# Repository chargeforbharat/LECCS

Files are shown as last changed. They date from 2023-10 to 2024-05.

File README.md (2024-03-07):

# LECCS repository 

## Introduction
 
'Light Electric Combined Charging System' is an open source charging standard aimed at making interoperability of charging easy and seamless.
LECCS is the charging standard comprising of two parts

1. Connector specification  
    * Specified under IS-17017 : Part2 : Section 7  
2. Communication protocol  
    * Specified under IS17017 : Part 31   

## License and usage
 LECCS repository is the collection of information such as links to connector specification, specification documents (drawings, CAD), related firmware/software SDKs etc, for LECCS.  
 LECCS is one of the standards adopted by the Charge For Bharat consortium.  

 Copyright &copy; 2023 LECCS - Light Electric Combined Charging System

 This repository contains free information: you can redistribute it and/or modify
 it under the terms of the GNU General Public License as published by
 the Free Software Foundation, either version 3 of the License, or
 (at your option) any later version.  
 This repository is distributed in the hope that it will be useful,
 but WITHOUT ANY WARRANTY; without even the implied warranty of
 MERCHANTABILITY or FITNESS FOR A PARTICULAR PURPOSE.  
 See the GNU General Public License for more details.
 You should have received a copy of the GNU General Public License  along with this repository.  If not, see [https://www.gnu.org/licenses/]

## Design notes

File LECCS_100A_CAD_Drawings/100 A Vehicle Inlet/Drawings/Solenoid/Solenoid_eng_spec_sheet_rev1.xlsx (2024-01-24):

 |  | Main Specifications
S# | Specification | Description | Typical / Standard | Min | Max | Units
Functional
1 | Operating Voltage | DC voltage polarity reversed on the same wires for lock and unlock | 12 | 9 | 12.5 | V
2 | Operating Current | Pulse (<300 ms) | - | - | 3 | A
3 | Holding Force/Releasing Force | Solenoid Actuation Force | 10 | 7 | 12 | N
4 | Plunger Displacement |  | 5 |  |  | mm
5 | Plunger Length (unlock) | From the mounting surface | 7.5 | 7.3 | 7.8 | mm
6 | Plunger Length (lock) | From the mounting surface | 12.5 | 12.3 | 12.8 | mm
7 | Plunger diameter |  | 4 |  |  | mm
8 | Failure force | Failure of plunger in case of abuse | 45 |  |  | kg
9 | Feedback Switch | Actuated during ON/OFF for state recognition (lock & unlock) | - | - | - | -
10 | Feedback Switch Operating states | Solenoid in Lock | Contact Closed | - | - | -
11 |  | Solenoid in Unlock | Contact Open | - | - | -
12 | Feedback Switch applied Voltage |  | 3.3 |  |  | V
13 | Feedback Switch applied Current |  | - | 0.5 | 100 | mA
14 | Feedback Switch Resistance | Open State | - | 1 | - | M Ohms
15 |  | Close State | - |  | 0.2 | Ohms
16 | Manual Operation | Manual override | - | - | - | -
17 | Manual Override operating force | Lever pulling force | 10 | 7 | 12 | N
Environmental
1 | Ingress Protection | Part level | IP 54 | - | - | -
3 | Operating Temperature |  | 30 | -20 | 70 | °C
4 | Random Vibration | 10 years of use with no critical failures with on road vibrations. Tested as per Indian city conditions |  |  |  | ATS26
5 | Mechanical Shock | 10 years of use with no critical failures with potholes and curb stones Tested as per Indian city conditions |  |  |  | ATS 11
6 | Corrosion | 5 years of use with no user noticable degradation 10 years of use with no critical failures Tested as per worst Indian coastal city conditions |  |  |  | ATS23
7 | Resistane to vehicle fluids | Protection against Petrol/Diesel, Greases, Vehicle washing chemicals, Transmission fluids, Engine oil etc. | - | - | - | -
8 | Dielectric breakdown Strength (For Switch only) | 100V rms applied for 60 seconds across two terminals | Flash-over shall not occur | - | - | -
9 | Insulation Resistance Test - For Switch (b/w body and terminal) | 500V DC applied for 10 seconds | - | 1 | - | MΩ
Safety
1 | Breakdown voltage (For Switch only) | 100V rms applied for 60 seconds across two terminals | Flash-over shall not occur
2 | Insulation Resistance (For Switch only) | 500V DC applied for 10 seconds wrt Charging pannel |  | 1 |  | MΩ
Operating Modes
1 | Powered | Charging ON | Lock | - | - | -
 |  | Charging OFF | Unlock
2 | Manual | Override manual actuation/Charging OFF | Unlock | - | - | -
Compliance
 | AIS 138 | Vehicle level only
Protections
1 | Freefall damage protection | Freefall damage protection during assembly and handling | - | - | - | Drop from 3 feet height in all six directions
2 | Damage protection | Damage protection during shipping and Storage | - | - | - | Shipping Random vibration test as per ASTM D4728/ISTA 3A and Drop test as per ASTM D4728/ISTA 3A
3 | Fire Protection | Fire resistance materials |  |  |  | Flamability Test UL 94 V-1
Interactions & Communications
 | NA
Realibility
1 | ON OFF Cycles |  |  | 10000 |  | Cycles
2 | Lifetime |  |  | 10 |  | Years
3 | IPHV | Issues per 100 units over lifetime | 1
Serviceability
1 | Service center Replaceable
2 | Field resetable (Manual override)
All others
1 | Wire Pull force | Wire to Casing and Connector | - | 5 | - | Kg
2 | Connector | Besmak 4MW 090 FHCL (BLACK)
3 | Individual Wire Cross Section | FLYR B, PVC, 100deg C | 0.35 |  |  | sqmm
4 | Individual Wire Insultion dia | FLYR B, PVC, 100deg C | 1.3 | 1.2 | 1.4 | mm
5 | Terminal | TT 1378
6 | Connector seal | 281934-4
7 | Wire legth | Wire length (Connector length excluded) | 250 | 240 | 260 | mm
8 | Wire colors | Drawing Attached
9 | Pin Maping | Drawing Attached
10 | Core cable specifications | Diameter | 5 | 4.8 | 5.2 | mm
11 | Reset wire length | Wire Length | 150 | 135 | 165 | mm
12 | Lock/Unlock Sound | TBD
13 | Torque | Screw tightening torque | 0.5 | 0.4 | 0.6 | N-m
14 | Weight | Solenoid assembly weight with Pigtail |  |  | 80 | gm

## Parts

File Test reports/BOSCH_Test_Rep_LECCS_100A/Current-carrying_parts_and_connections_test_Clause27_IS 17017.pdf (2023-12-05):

From | Our reference | Phone | E-Mail
MS/ENB3 | Prijo Ulahannan | +91 80 6783 6100 | Prijo.ulahannan@in.bosch.com | Date: 18-Aug-2022 Report No.: Ather_06_TR
Page 1 of 4 Confidential | Test Report | © BGSW reserves all rights even in the event of industrial property rights.

We reserve all rights of disposal such as copying and passing on to third parties.
Report template V1 (05/25/2022)
Report: | Test report
Title: | Current-carrying parts and connections test
Customer: | Ather India

Document approval

| Name | Signature | Version
Prepared by | Prijo Ulahannan | | 1.0
Reviewed by | Mahantesh Ramannavar

### 1. Issues (situation, motivation and tasks)

The Ather Company has designed and developed a charging connector for electric vehicles, which is patented. Ather has approached Bosch (BGSW) to validate the charging connector between the vehicle and the charging station according to IS 17017 selective tests as prescribed by Ather requirements.

Current-carrying parts, other than terminals (Wire element) were used for test. The task was to check the current-carrying parts, other than terminals which is used and criteria are as per IS 17017 chapter no.27.5 to check the functionality of the samples.

### 2. Results, short version

| | o.k. | not o.k.
2.1 | Material properties of current-carrying parts, other than terminals (Wire) | ☒ | ☐

The overall result of the examined samples is:

☒ Positive
☐ Negative: No further analysis required

Recommendation for further work: NA

MS/ENB3 | Prijo Ulahannan | +91 80 6783 6100 | Prijo.ulahannan@in.bosch.com | Date: 18-Aug-2022 Report No.: Ather_06_TR
Page 2 of 4 Confidential | Test Report | © BGSW reserves all rights even in the event of industrial property rights.

### 3. Conclusions and consequences

All samples have passed the test. All the test parameters are within the specified limit of assessment criteria.

### 4. Results, long version

4.1 Material properties of current-carrying parts, other than terminals – OK (See chapter 5.4 for criteria)

4.1.1 Shall be either of copper.

4.1.2 An alloy containing at least 50 percent copper.

### 5. Details

### 5.1 Part details:

Sl. No. | Description | Part number | Manufacture date / Received date | Remarks
1 | FLRYB 25 Sqmm | ----- | July-2022 | -
2 | FLRYB 0.5 Sqmm | ----- | July-2022 | -

### 5.3 Sample preparation, test setup and test details:

1. Visual inspection of all the samples before test.
2. Visual inspection of samples for the material checks under microscope performed.
3. Data sheet for the wire is checked for material used.
4. Martial composition check has made under X-Ray scope.
5. Same procedure was followed for the all the other samples.
6. See chapter 6 enclosure for more details

### 5.4 Test conditions and assessment criteria:

### 5.4.1 Material properties current-carrying parts, other than terminals

Current-carrying parts, other than terminals, shall be either of,
a) Copper.
b) An alloy containing at least 50 percent copper
c) Other metal no less resistant to corrosion than copper and having mechanical properties no less suitable.

Compliance is checked by inspection if need chemical analysis.

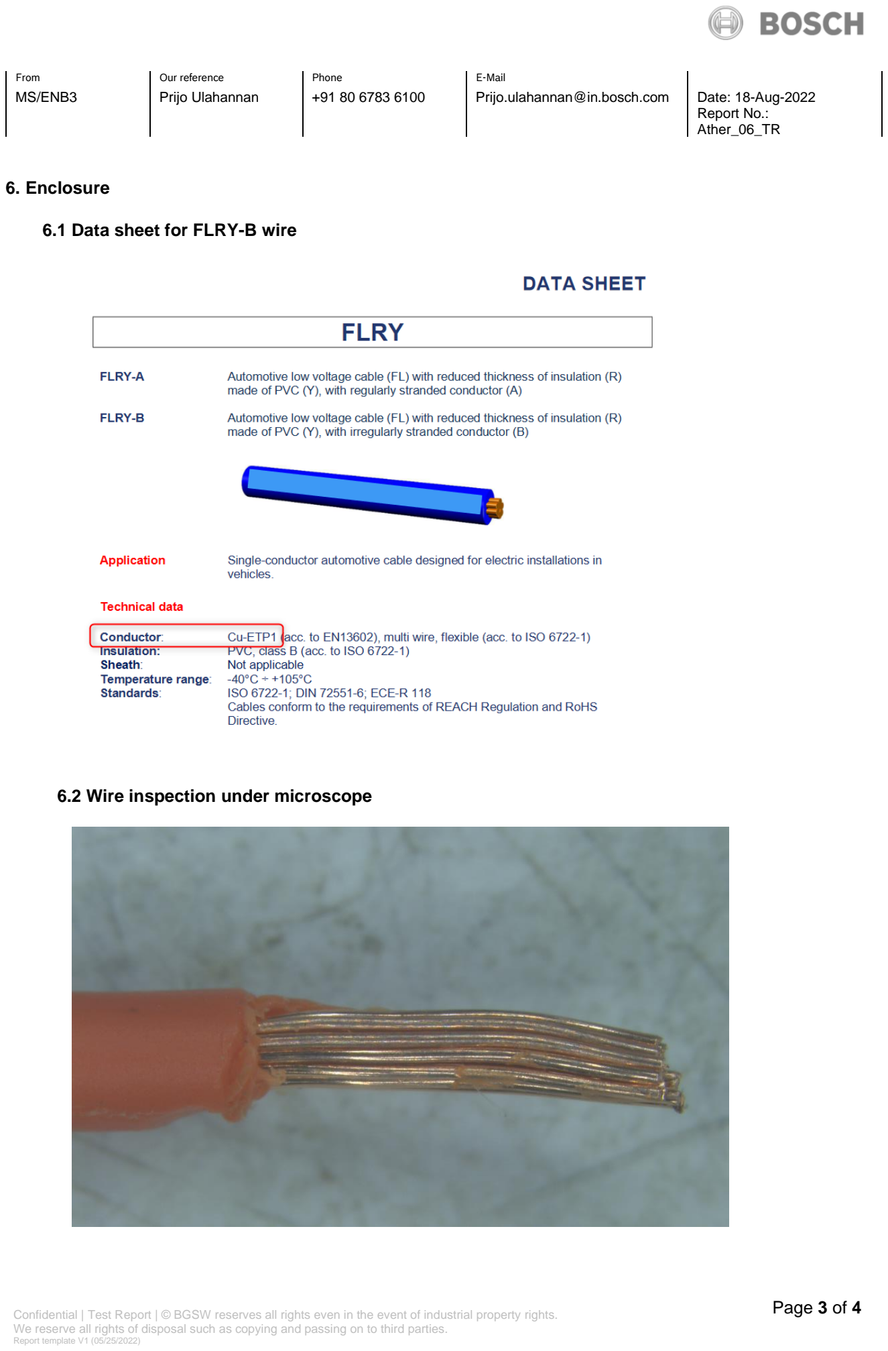
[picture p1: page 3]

MS/ENB3 | Prijo Ulahannan | +91 80 6783 6100 | Prijo.ulahannan@in.bosch.com | Date: 18-Aug-2022 Report No.: Ather_06_TR
Page 3 of 4 Confidential | Test Report | © BGSW reserves all rights even in the event of industrial property rights.

### 6. Enclosure

### 6.1 Data sheet for FLRY-B wire

### 6.2 Wire inspection under microscope

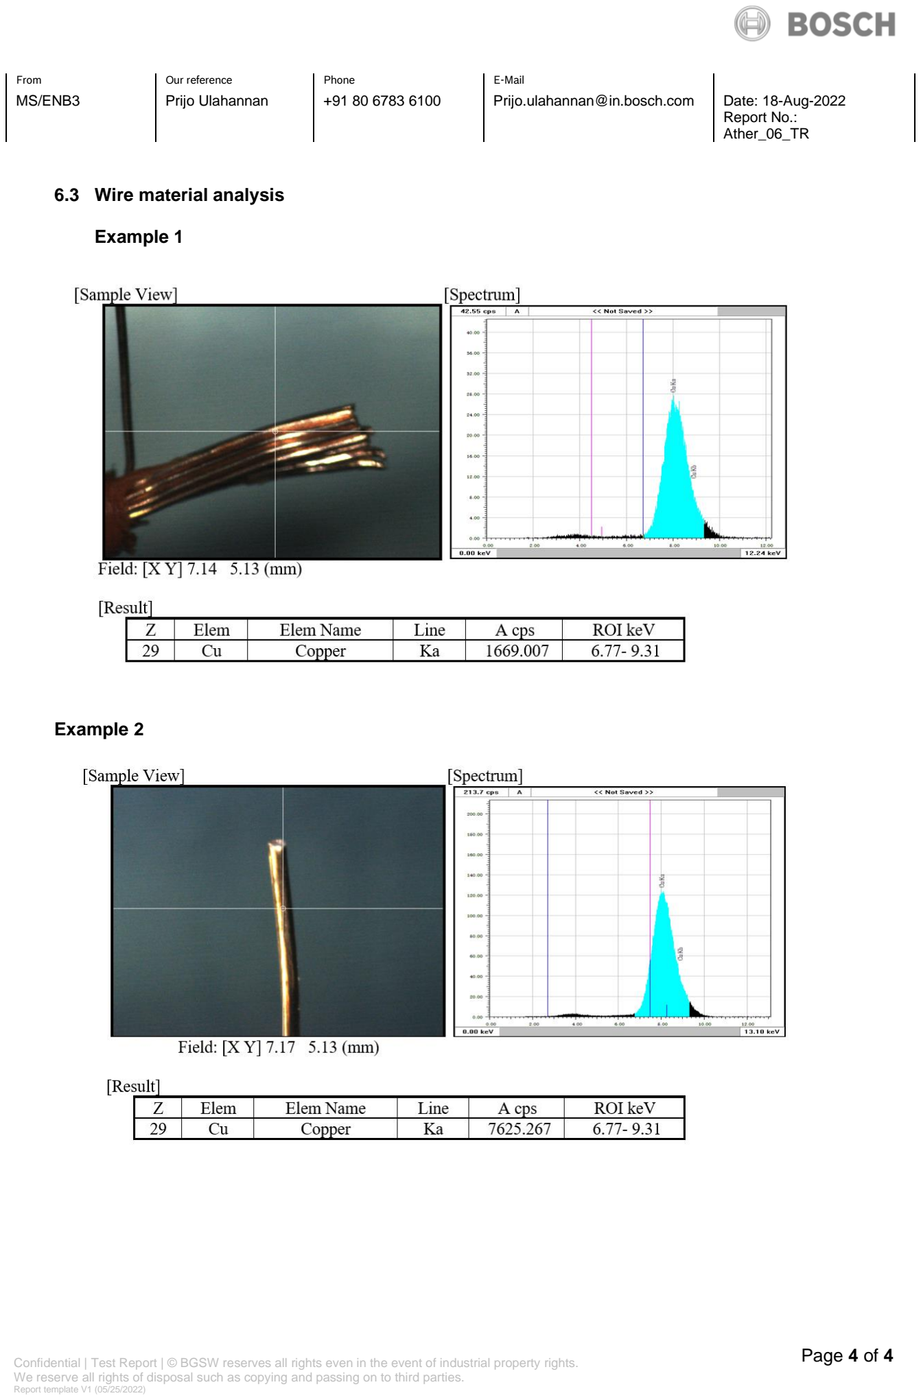
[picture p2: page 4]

MS/ENB3 | Prijo Ulahannan | +91 80 6783 6100 | Prijo.ulahannan@in.bosch.com | Date: 18-Aug-2022 Report No.: Ather_06_TR
Page 4 of 4 Confidential | Test Report | © BGSW reserves all rights even in the event of industrial property rights.

### 6.3 Wire material analysis

Example 1

Example 2

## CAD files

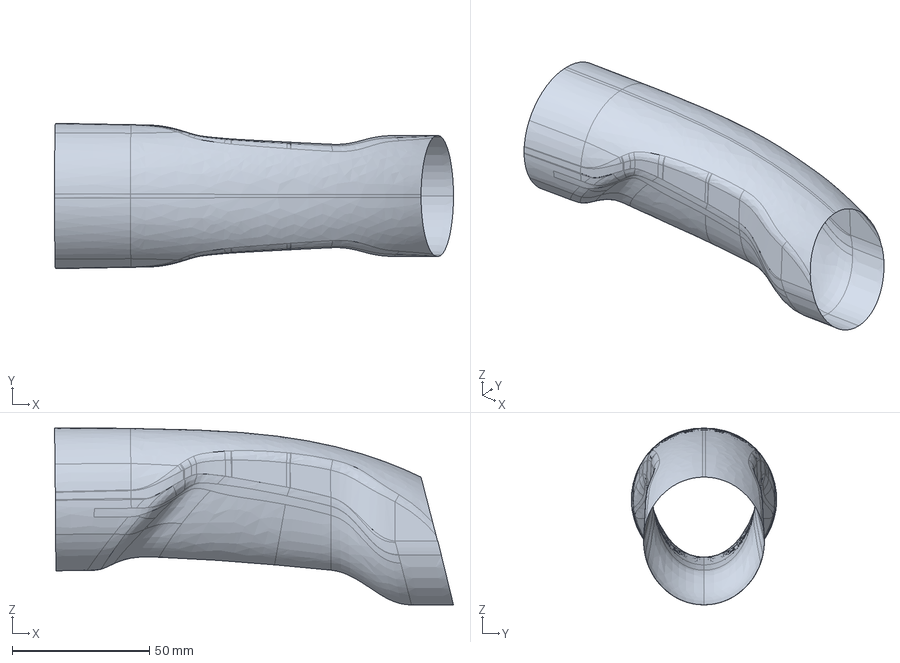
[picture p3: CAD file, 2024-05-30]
LECCS_100A_CAD_Drawings/100 A Charging Handle/Charging Handle/Handle surface.igs
145.5 x 53.0 x 64.5 mm

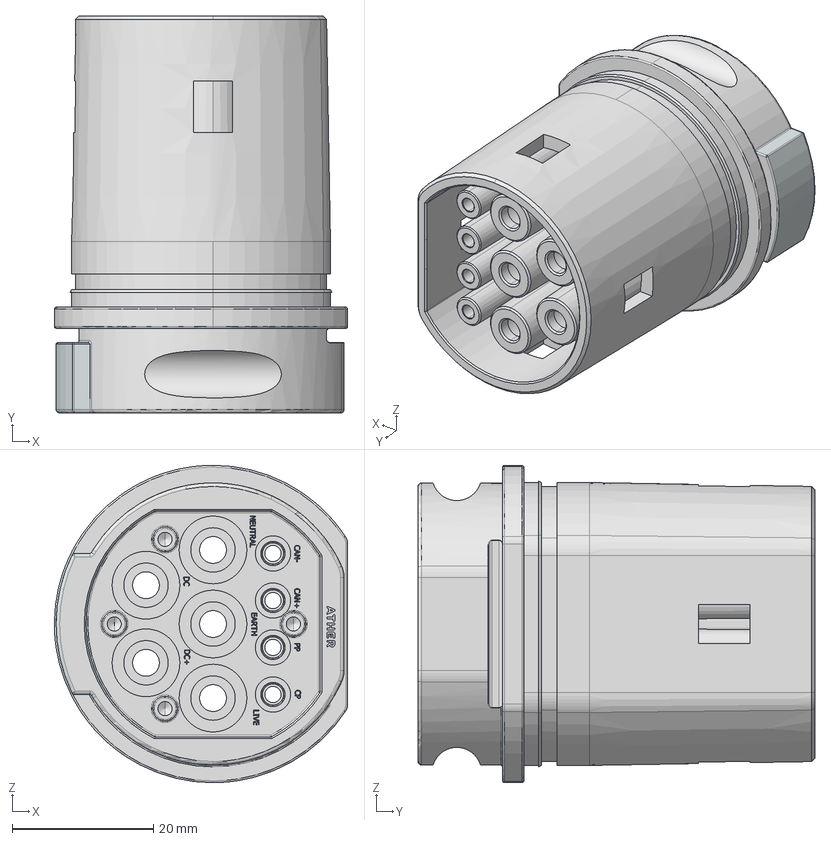
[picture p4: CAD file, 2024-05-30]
LECCS_100A_CAD_Drawings/100 A Charging Handle/Charging Handle/BE5101A004ANN_D_STEP (1).stp
41.6 x 56.3 x 45.0 mm

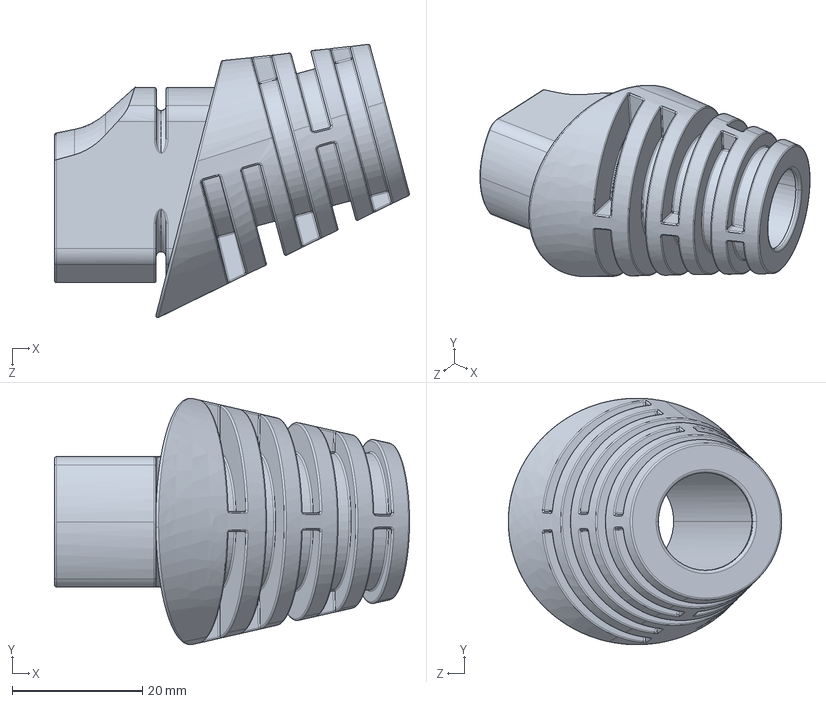
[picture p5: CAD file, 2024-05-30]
LECCS_100A_CAD_Drawings/100 A Charging Handle/Charging Handle/PB00000641-02.STEP
54.5 x 37.8 x 42.0 mm

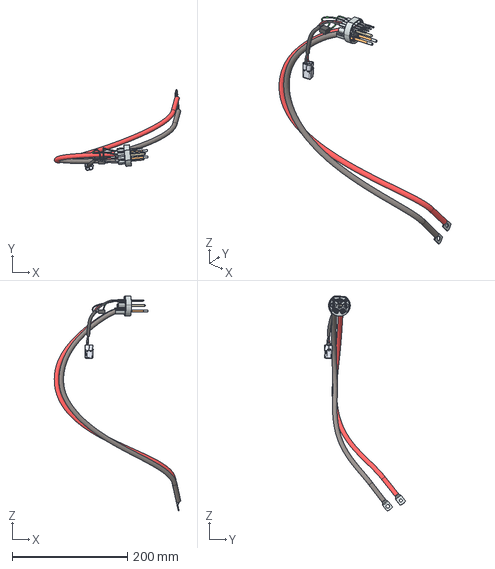
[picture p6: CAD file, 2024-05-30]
LECCS_100A_CAD_Drawings/100 A Vehicle Inlet/CAD/EP00000127_03_STEPSelected_Objs.stp
219.9 x 141.0 x 373.7 mm

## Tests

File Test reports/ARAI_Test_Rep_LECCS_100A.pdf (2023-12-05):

DEVELOPMENT TEST REPORT | CONFIDENTIAL

Report No. ARAI/AED/20222023/3100013430/DT/5075
Dated: 27-JUN-2022
1.0 Name and Address of the | Customer | M/s. ATHER ENERGY PRIVATE LIMITED 3RD FLOOR TOWER D, IBC KNOWLEDGE PARK, BANNERGHATTA MAIN ROAD, BANGALORE-560029, KARNATAKA, INDIA
2.0 | Customer Letter Reference | Email dated: 21-MAR-2022
3.0 | Test Objective | Testing of DC EV vehicle connector (charging gun) and vehicle inlet (for light electric vehicles) according to IS 17017-2-1.
4.0 Condition of the Test | Component | The test components were received in good condition.
5.0 Description of the Device Under | Test (DUT) | DC EV Charging gun and Vehicle inlet
5.1 | Make | Ather Energy Private Limited
| Part numbers | 340A0021532, 340A0021531
DUT Photos

6.0

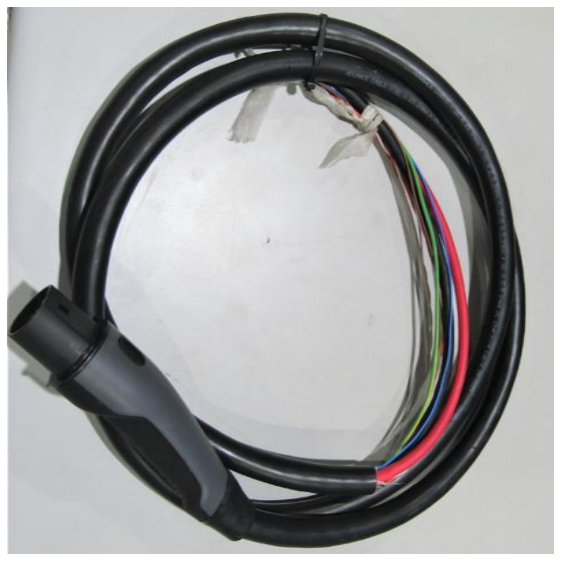
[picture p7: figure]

Result:

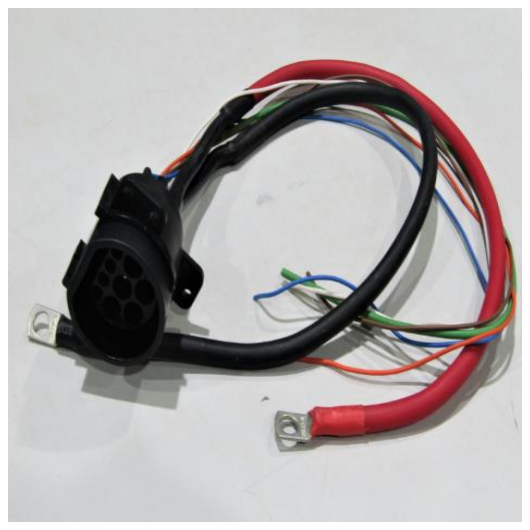
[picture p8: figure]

The DC EV Charging gun and vehicle inlet (for light electric vehicles) serial numbers: “340A0021532, 340A0021531” meets the requirements as per clause 8.0(Test results) of this report

A A MURUMKAR
ENGINEER

A B MULAY
GENERAL MANAGER

A A DESHPANDE
Sr. Dy. DIRECTOR & HoD

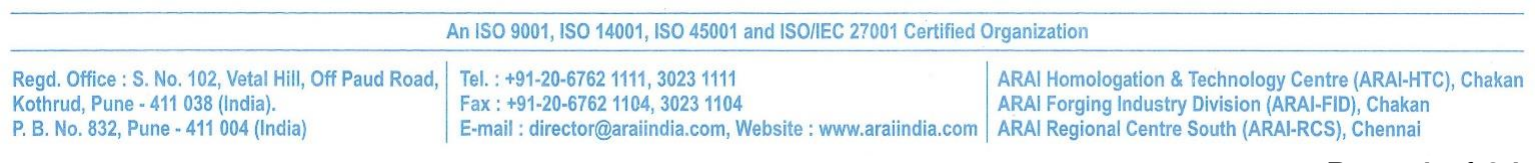
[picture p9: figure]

Report No. ARAI/AED/20222023/3100013430/DT/5075 | CONFIDENTIAL
Dated: 27-JUN-2022

### 7.0 DUT Details:

General product information:
The DUT submitted for the test is a DC EV charging gun and vehicle inlet for Light electric vehicles, Ratings:120V DC Max, 100Amp DC Max current
Number of poles: 9 poles (CP, PP, CAN HIGH, CAN LOW, DC+, DC-, PE) + 2 dummy poles

### 8.0 Test Results:

Sr. No | Test Title | Annex No. | Complies (Yes/No/ N/A)
1.0 Tests and verifications as per IS17017-2-1 | Clause no 10 of this report. | -- | Yes
2.0 | Electrical tests as per IS17017-2-1. | 01 | Yes
3.0 | Environmental/ Climatic tests as per IS17017-2-1. | 02 | Yes
4.0 | Mechanical tests | 03 | Yes

A A MURUMKAR
ENGINEER

A B MULAY
GENERAL MANAGER

_______________________________________________________________________________

This test report pertains only to the components / parts / assemblies / vehicles etc., actually tested at ARAI in the presented condition based on the documents / information produced / submitted by the customer. The issuance of this test report alone does not indicate any measure of approval, certification, supervision, control of quality surveillance by ARAI of the product. No extract, abridgement or abstraction from this test report shall be published or used to advertise the product without the written consent of the Director, ARAI, who reserves the absolute right to agree or reject all or any of the details of any items of publicity for which consent may be sought. ARAI is in no way responsible for any misuse of copying of any design / type / system in connection with entire vehicle/components/parts and assemblies. Breach of any statutory provision of Indian laws or laws of other countries, will be the sole responsibility of the customer and ARAI shall not be liable for any claims or damages, made by the party, whatsoever. The customer shall alone be liable for the same and undertakes to indemnify ARAI in this regard. Further, the ARAI has the right to initiate cancellation / withdrawal of the certificate / report issued, in case of any fraud, misrepresentation, when it surfaces and comes in the knowledge of ARAI. The appropriate local courts at Pune shall have the jurisdiction in respect of any dispute, claim or liability arising out of this report.
Place of Issue: ARAI-HTC, Pune

### 9.0 Connector Photos:

Charging gun Part no: 340A0021532 | Vehicle Inlet Part no: 340A0021531

Markings:

A A MURUMKAR
ENGINEER

A B MULAY

GENERAL MANAGER

### 10.0 Requirements as per IS17017-2-1

Sr. no | Test requirement/specifications | Observation/Remark
1 | Ratings
1.1 | Preferred rated operating voltage ranges: | 120VDC Max
1.2 | Preferred Rated Currents | 100A DC Max
1.3 | Rated Current for Signal or Control Purposes | Rated current for signal or control purposes is 2 A.
1.4 | Accessories suitable or not Suitable for Making and Breaking an Electrical Circuit Under Load | Not suitable for making and breaking an electrical circuit under load
1.5 | Accessories Suitable for, or not Suitable for, Making and Breaking an Electrical Circuit Under Load | Complies
1.6 | Connection between the power supply and the electric vehicle:
2 | General
2.1 | Types of Vehicle Connectors | DC EV Charging gun and vehicle inlet, as declared by customer
2.2 | Basic Interface | DC interface as declared by customer

A A MURUMKAR
ENGINEER

A B MULAY
GENERAL MANAGER

Sr. no | Test requirement/specifications | Observation/Remark
3 | Classification of Accessories
3.1 | According to the Method of Connecting the Conductors | Non-rewireable
3.2 | According to Serviceability | Non-serviceable accessories
3.3 | According to Electrical Operation | Accessories not suitable for making and breaking an electrical circuit under load
3.4 | According to Interface | DC interface, as declared by customer
3.5 | According to the Locking and Interlock Functions
3.6 | According to Locking Facilities | Lockable means provided.
3.7 | According to Interlock Facilities | Means of latching provided, Interlock on vehicle side
3.8 | According to the Presence of Shutter(s) | Without shutters
4 | Marking
4.1 | Accessories shall be marked with: a) Rated current(s) in amperes for power, b) Rated maximum operating voltage(s) in volts, c) The relevant symbol for degree of protection, d) Either the name or trade mark of the manufacturer | Markings provided

A A MURUMKAR
ENGINEER

A B MULAY
GENERAL MANAGER

Sr. no | Test requirement/specifications | Observation/Remark
4.2 | For vehicle connectors, the marking for either the name or trade mark of the manufacturer or the responsible vendor and the type reference, catalogue number or designation shall also be on the outside of the accessory, visible to the user. | Markings provided
4.3 | For all accessories, the marking for the maximum rated operating voltage range and rated current shall be in a place which is visible before installation of the accessory. | Markings provided
4.4 | Markings shall be indelible and easily legible. | Compiles
5 | Dimensions
5.1 | Accessories shall comply with the appropriate standard sheets | Customer specific design for light electric vehicles DC charging. Drawings sheet provided by the customer
5.2 | It shall not be possible to engage vehicle connectors with vehicle inlets having different ratings, or having different contact combinations unless safe operation is ensured or other means are provided to ensure safe operation. | Complies

A A MURUMKAR
ENGINEER

A B MULAY
GENERAL MANAGER

Sr. no | Test requirement/specifications | Observation/Remark
6 | Protection against electric shock
6.1 | Accessories shall be so designed that live parts of vehicle connectors, when they are wired as in normal use, and live parts of plugs and vehicle inlets, when they are in partial or complete engagement with the complementary accessories, are not accessible. | Complies Live parts not accessible.
6.2 | Accessories shall be so designed that, it should follow contact sequencing for connection and disconnection of vehicle connector | Complies
6.3 | It shall not be possible to inadvertently assemble either the part carrying plug or inlet contacts into the enclosure of a socket-outlet or vehicle connector or the part carrying the vehicle connector contacts into the enclosure of a plug or inlet. | Assemblies are Non-rewireable
7 | Size and colour of protective earthing conductors
7.1 | The conductor connected to the protective earthing terminal shall be identified by the colour combination green-and-yellow. | 2.5 sqmm protective conductor provided.
7.2 | The nominal cross-sectional area of the protective earthing conductor and of the neutral conductor,

A A MURUMKAR
ENGINEER

A B MULAY
GENERAL MANAGER

Sr. no | Test requirement/specifications | Observation/Remark
8 | Provision for Earthing
8.1 | Accessories are provided with a protective earthing contact and a protective earthing terminal. | Provided
8.2 | Protective earthing contacts are directly and reliably connected to the protective earthing terminals. | Complies
8.3 | Earthing contacts are shrouded or guarded against mechanical damage | Complies
9 | Accessories with interlock
9.1 | Accessories classified in “not suitable for making and breaking an electrical circuit under load” shall be provided with an interlock. | Interlock provided
9.2 | Vehicle couplers with interlocks shall be so constructed that:
9.2.1 | a vehicle connector cannot be completely withdrawn from the vehicle inlet while the contacts of that vehicle connector are live | Complies
9.2.2 | the contacts of the vehicle connector cannot be made live until the vehicle connector is in proper engagement
9.2.3 | The power contacts shall not make or break under load

A A MURUMKAR
ENGINEER

A B MULAY
GENERAL MANAGER

Sr. no | Test requirement/specifications | Observation/Remark
9.3 | Pilot Contacts and Auxiliary Circuits
9.3.1 | Pilot contacts and auxiliary circuits used for interlocks shall make after the neutral and phase(s) are made. | Complies
9.3.2 | Pilot contacts and auxiliary circuits used for interlock shall break before the phase(s) and neutral are broken. | Complies
10 | General Construction
10.1 | Accessible surfaces of accessories shall be free from burrs, flashes and similar sharp edges. | No sharp edges, burrs
10.2 | Vehicle connectors when mounted as in normal use and without a plug and vehicle inlet respectively in position shall ensure the degree of protection specified on its marking. | Complies
10.3 | Contacts shall be so designed as to ensure adequate contact pressure when completely engaged with the corresponding accessory | Complies
10.4 | Enclosures and parts of accessories providing protection against electric shock shall have adequate mechanical strength | Complies
10.5 | It shall not be possible to remove these parts without the aid of a tool. | Complies
10.6 | Cable entries shall allow the introduction of the conduit or the protective covering of the cable to afford complete mechanical protection. | Complies

A A MURUMKAR
ENGINEER

A B MULAY
GENERAL MANAGER

Sr. no | Test requirement/specifications | Observation/Remark
10.7 | Insulating linings, barriers and the like shall have adequate mechanical strength. | Complies
10.8 | A gripping surface shall be provided | Provided
11 | Construction of Vehicle connectors
11.1 | The enclosure of vehicle connectors shall completely enclose the terminals and the ends of the flexible cable. | Complies
11.2 | Parts of a connector do not work loose during normal use | No loosening observed
11.3 | Connectors cannot be dismantled without a tool | Complies
11.4 | Vehicle connectors incorporate means to meet the marked degree of protection when engaged with the vehicle inlet | Complies
11.5 | Means provided to meet the marked degree of protection are securely fixed to the connector | Complies
12 | Degree of Protection
12.1 | IP rating marked on device | IP44
12.2 | All accessories shall be proof against humid conditions which may occur in normal use. | Complies
13 | Insulation resistance and dielectric strength
13.1 | Insulation resistance | Resistance observed R>5MΩ
13.2 | Dielectric Strength test | Test performed at 2kV, No break down or flashover observed

A A MURUMKAR
ENGINEER

A B MULAY
GENERAL MANAGER

Sr. no | Test requirement/specifications | Observation/Remark
13.3 | Normal Operation
13.3.1 | Normal operation cycles in no load 10,000 cycles | After test observation: 1. No detached part 2. No deterioration of enclosures or barriers; 3. No damage to the entry holes for the plug contacts that might impair proper working 4. No loosening of electrical or mechanical connections 5. No seepage of sealing compound 6. The continuity between mating signal and pilot contacts are maintained.
14 | Flexible cable and their connection
14.1 | Vehicle connectors shall be so designed that the conductors are relieved from strain, including twisting, where they are connected to the terminals or terminations, and that their covering is protected from abrasion. | Flexible cables provided
14.2 | The construction shall ensure that the cable cannot touch accessible metal parts or internal metal parts | Complies
15 | Requirements for vehicle connectors
15.1 | Non-rewireable vehicle connectors
15.1.1 | Non-rewireable vehicle connectors shall be provided with a suitable flexible cable | Provided

A A MURUMKAR
ENGINEER

A B MULAY
GENERAL MANAGER

Sr. no | Test requirement/specifications | Observation/Remark
16 | Mechanical strength
16.1 | Accessories shall have adequate mechanical strength so as to withstand the stresses imposed during installation and use. | Complies
17 | Change of temperature test
17.1 | Temperature test of IEC 60068-2-14, test procedure Nb | See Annexure no: 02 No deformation observed
18 | Resistance to heat
18.1 | Accessories are resistant to heat | See Annexure no: 02 No impairing was observed. Markings still visible after the test
18.2 | Devices are heated in cabinet for 1 hour at a temperature of 110 + 5°C and comply with all criteria at the end of the exposure
19 | Vehicle drive over
19.1 | A plug or vehicle connector shall have adequate resistance to damage from being driven over by a vehicle | See Annexure no: 03. No severe cracking, breaking or deformation observed
19.2 | Accessories wired with the min. size cable of a type recommended by the manufacturer shall be placed on a concrete floor in any normal position of rest
20 | Ratings
20.1 | A component shall be used in accordance with its rating established for the intended conditions of use | Complies
20.2 | Mechanical Assembly
20.2.1 | Loosening of parts in an accessory as a result of vibration due to storage, handling and operation shall not result in a risk of fire, electric shock, injury to persons | Complies

A A MURUMKAR
ENGINEER

A B MULAY
GENERAL MANAGER

ANNEXURE 01

### 1.1 TEST SPECIFICATIONS

TEST DETAILS | ELECTRICAL TESTS AS PER IS 17017-2-1
TEST LOCATION | AED, ARAI-HTC

### 1.2 LABORATORY ENVIRONMENT TEST CONDITIONS

Ambient
temperature | + 25.5°C. | ---- | Relative humidity | 48.5%RH. | ----

### 1.3 INSULATION RESISTANCE AND DIELECTRIC WITHSTAND TEST

Test date: 25-MAR-2022
Test Requirement:
The insulation resistance shall be not less than 5 MΩ.
Dielectric withstand test at 2000V, No flashover or breakdown shall occur during the test. Insulation resistance (IR) test results/observation:
Test parameters | Test voltage applied | Observation
Between all poles connected together and the body | 500 | IR ≥ 5 MΩ
Between each pole in turn and all others, these being connected to the body | 500 | IR ≥ 5 MΩ

Dielectric withstand test results/observation:

Test parameters | Test voltage applied | Observation
Between all poles connected together and the body | 2000 | No flashover or breakdown observed during the test.
Between each pole in turn and all others, these being connected to the body | 2000 | No flashover or breakdown observed during the test.

A A MURUMKAR
TEST ENGINEER

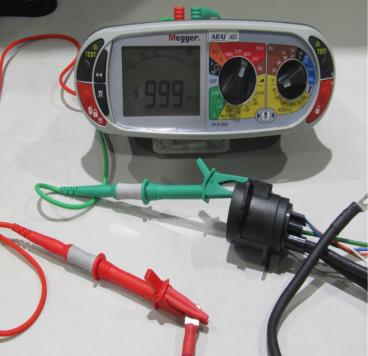
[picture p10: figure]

### 1.4 Temperature Rise test as per IS17017-2-1

Test Date: 25-MAR-2022

### 1.4.1 Test Requirements/Parameters:

1. Test performed at rated 100VDC, 100Amp current for 1 hour as declared by the manufacturer, to measure the temperature rise.
2. Test setup was done as per the normal use case of the vehicle inlet and the charging gun.
3. The maximum permissible temperature of those parts of the plug and the vehicle connector that can be grasped during normal operation, when tested with the accessory carrying the maximum rated current, shall not exceed
- 50 °C for metal parts,
- 60 °C for non-metal parts.
4. For parts which may be touched but not grasped the permissible temperature are
- 60 °C for metal parts,
- 85 °C for non-metal parts.

### 1.4.2 Test setup:

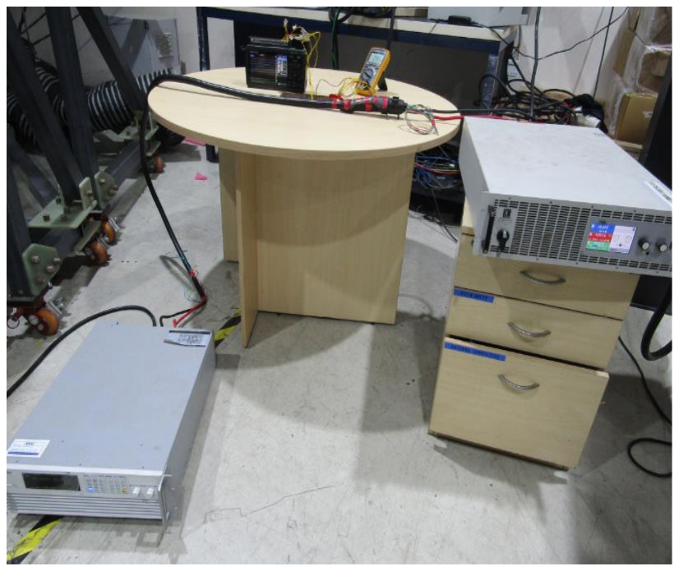
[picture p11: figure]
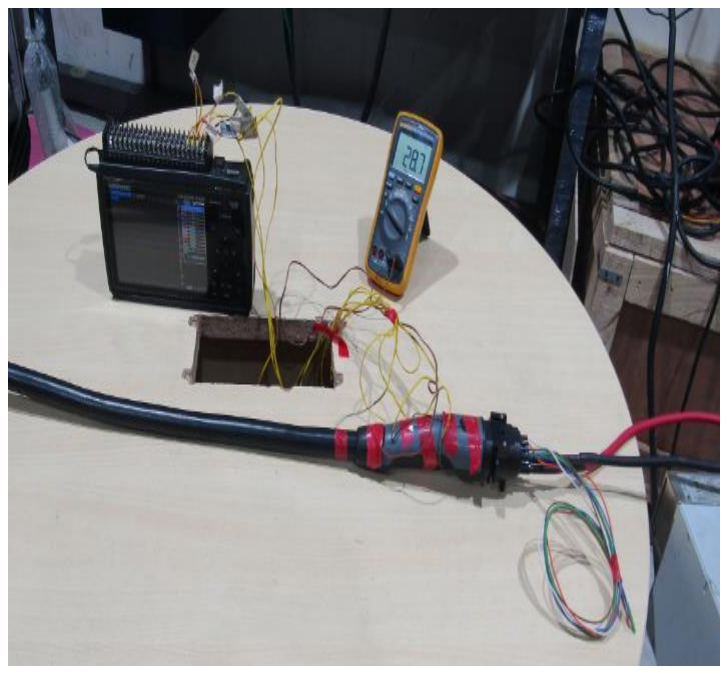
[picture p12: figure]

A A MURUMKAR
TEST ENGINEER

### 1.4.3 Test Result:

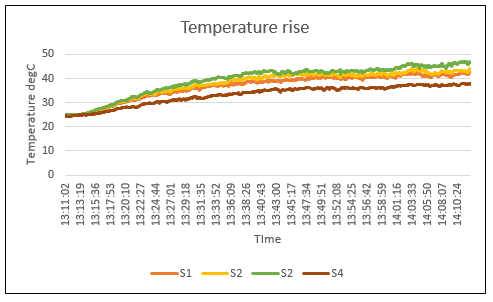
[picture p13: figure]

1.4.4Test observation:

1. The temperature rise of terminals did not exceed 50 degC
2. Surface temperature in normal use meets the requirements as per clause 1.4.1

A A MURUMKAR
TEST ENGINEER

### 1.5 CONTACT SEQUENCE TEST

Test date: 25-MAR-22
Test Requirement:
To check contact sequence of the control and power pins
Test Result/Observation:
The contact sequence observed while inserting the vehicle connector is: First contact: Protective earthing (PE)
Second contact: DC Power contacts (DC+ and DC-)
Third contact: Proximity detection (PP)
Fourth contact: Control pilot (CP) and CAN pins (CAN HIGH, CAN LOW)

While withdrawing the vehicle connector:
First release: Control pilot (CP) and CAN pins (CAN HIGH, CAN LOW) Second release: Proximity detection (PP)
Third release: DC Power contacts (DC+ and DC-)
Fourth release: Protective earthing (PE)

Contact sequencing achieved with different terminal lengths in-order to meet the requirements as

per standard.
Contact terminals photos:
Charging gun terminals: | Vehicle inlet terminals:

A A MURUMKAR
ENGINEER

A B MULAY
GENERAL MANAGER
End of Annexure 01

ANNEXURE 02

### 2.1 TEST SPECIFICATIONS

TEST DETAILS | ENVIRONMENTAL/CLIMATIC TESTS AS PER IS 17017-2-1
TEST LOCATION | AED, ARAI-HTC

### 2.2 LABORATORY ENVIRONMENT TEST CONDITIONS

Ambient
temperature | + 25.5°C. | ---- | Relative humidity | 48.5%RH. | ----

### 2.3 CHANGE OF TEMPERATURE TEST

Test date: 24-MAR-2022

Test Requirement:
Accessories with insulated end cap on the contacts shall not be adversely affected by the temperature stress conditions which may occur in normal use.

Test parameters:
Temperature test of IS 9000 (Part 14/Sec 2) with following parameters:
a) Test procedure: Nb;
b) Lower temperature (TA): -30°C;
c) Higher temperature (TB): 100°C;
d) Slew rate: 3 K/min;
e) Exposure time (t1): 1 h; and
f) Number of cycles: 5.

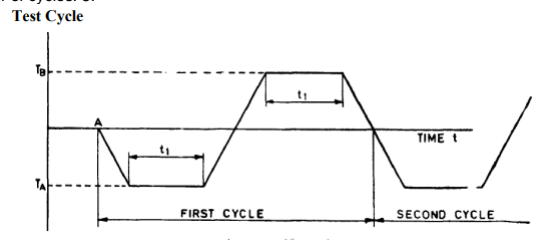
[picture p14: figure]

Test Result/Observation:
No deformation observed after the end of test

A A MURUMKAR
TEST ENGINEER

### 2.4 RESISTANCE TO HEAT TEST

Test date: 24-MAR-2022

Test Requirement:
Accessories shall be sufficiently resistant to heat.

Test parameters:
The samples are kept for 1 hour in a heating cabinet at a temperature of 110°C ± 5 K.

Test Result/Observation:
No impairing observed.
No sealing flow observed.
Markings are legible
Test Setup:

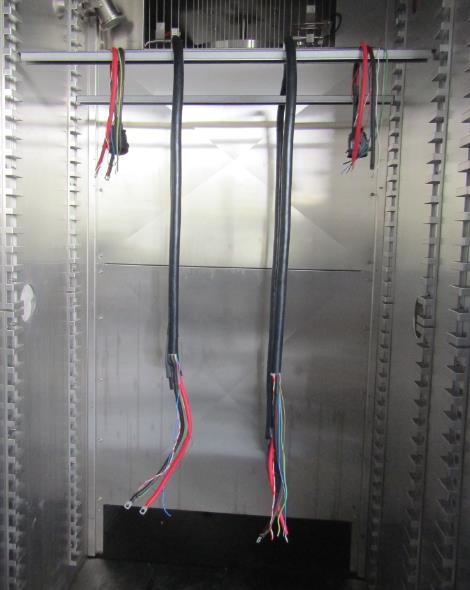
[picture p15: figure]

A A MURUMKAR
TEST ENGINEER

### 2.5 HUMIDITY STORAGE TEST

Test date: 05-APR-2022

Test Requirement:
All accessories shall be proof against humid conditions which may occur in normal use.

Test parameters:
The humidity treatment is carried out in a humidity cabinet containing air with a relative humidity maintained between 91 percent and 95 percent. The temperature of the air, at all places where samples can be located, is maintained within 1°C of any convenient value T between 20°C and 30°C for 168 hrs
After test:
Markings should be legible
Required IR ≥5MΩ
Test Setup:

Test result:

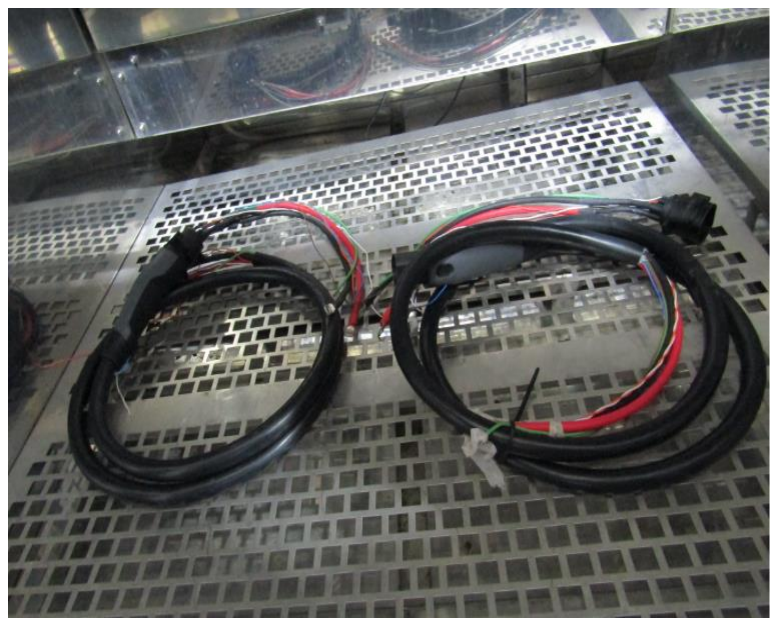
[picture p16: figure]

Measured IR was found to be ≥5MΩ
Markings are legible, and no impairing or sealant flow observed

A A MURUMKAR
TEST ENGINEER

A B MULAY
GENERAL MANAGER
End of Annexure 02

ANNEXURE 03

### 3.1 TEST SPECIFICATIONS

TEST DETAILS | MECHANICAL TESTS
TEST LOCATION | AED, ARAI-HTC

### 3.2 LABORATORY ENVIRONMENT TEST CONDITIONS

Ambient
temperature | + 25.5°C. | ---- | Relative humidity | 48.5%RH. | ----

### 3.3 VEHICLE DRIVE OVER TEST

Test date: 18-APR-2022
Test Requirement:
1. A plug or vehicle connector shall have adequate resistance to damage from being driven over by a vehicle, unless it is provided with a cable management system which prevents the accessory from being left on the ground.
2. The wheel is to be rolled over the vehicle connector or plug at a speed of 8 ± 2 km/h. The accessory is to be oriented in a natural resting position before applying the force in a different direction for each sample.
3. There shall be no severe cracking, breakage, or deformation.
Test photo:


A A MURUMKAR
TEST ENGINEER

Test Result/Observation:


1. No severe cracking, breakage, or deformation observed.
2. Measured IR after test was found to be ≥5MΩ.

### 3.4 DROP TEST

Test date: 25-MAR-2022
Test Requirement:
1. Drop test to be performed from a height of 1m on concrete surface, in all directions
2. There shall be no severe cracking, breakage, or deformation.
3. Test performed as per customer requirements
Test photo:


A A MURUMKAR
TEST ENGINEER

Test Result/Observation:


1. No severe cracking, breakage, or deformation observed.
2. Measured IR after test was found to be ≥5MΩ.

### 3.5 CONNECTOR RESISTANCE TO DRAG

Test date: 19-APR-2022
Test Requirement:
1. Drag of charging cable for 1km, to check the insulation and mechanical strength
2. There shall be no severe cracking, breakage, or deformation.
3. Test performed as per customer requirements
Test photo:


A A MURUMKAR
TEST ENGINEER


Test Result/Observation:


1. No severe cracking, breakage, or deformation observed.
2. Measured IR after test was found to be ≥5MΩ.

A A MURUMKAR
TEST ENGINEER

### 3.6 MARKINGS

Test date: 25-MAR-2022
Test Requirement:
1. Markings shall be indelible and easily legible
2. After the humidity treatment, the marking is rubbed vigorously by hand for 15 seconds with a piece of cloth soaked in water and again for 15 seconds with a piece of cloth soaked with petroleum spirit.
Test photo:


Test Result:


After test Markings are indelible and easily legible. Laser printed markings as declared by manufacturer

A A MURUMKAR
TEST ENGINEER


A B MULAY
GENERAL MANAGER
End of Annexure 03
--- END OF TEST REPORT---

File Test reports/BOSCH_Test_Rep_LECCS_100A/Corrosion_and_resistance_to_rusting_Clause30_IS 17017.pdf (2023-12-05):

From | Our reference | Phone | E-Mail
MS/ENB3 | Prijo Ulahannan | +91 80 6783 6100 | Prijo.ulahannan@in.bosch.com | Date: 18-Aug-2022 Report No.: Ather_01_TR
Page 1 of 4 Confidential | Test Report | © BGSW reserves all rights even in the event of industrial property rights.

We reserve all rights of disposal such as copying and passing on to third parties.
Report template V1 (05/25/2022)
Report: | Test report
Title: | Corrosion and resistance to rusting
Customer: | Ather India

Document approval

| Name | Signature
Prepared by | Prijo Ulahannan
Reviewed by | Mahantesh Ramannavar

### 1. Issues (situation, motivation and tasks)

The Ather Company has designed and developed a charging connector for electric vehicles, which is patented. Ather has approached Bosch (BGSW) to validate the charging connector between the vehicle and the charging station according to IS 17017 selective tests as prescribed by Ather requirements.

3 samples of vehicle connector and Vehicle inlet were used for test. The task was to expose the samples to a some of the solutions as specified in standard for a specified duration to check the behavior of connector in corrosive environment. Test and acceptance criteria are as per IS 17017 chapter no. 30 o check the functionality of the samples.

### 2. Results, short version

| | o.k. | not o.k.
2.1 | Visual inspection of plastic parts for cracks and breakage (New condition) | ☒ | ☐
2.2 | Visual inspection of samples for rust after test | ☒ | ☐

The overall result of the examined samples is:

☒ Positive
☐ Negative: No further analysis required

Recommendation for further work: NA

MS/ENB3 | Prijo Ulahannan | +91 80 6783 6100 | Prijo.ulahannan@in.bosch.com | Date: 18-Aug-2022 Report No.: Ather_01_TR
Page 2 of 4 Confidential | Test Report | © BGSW reserves all rights even in the event of industrial property rights.

### 3. Conclusions and consequences

All 3 connector samples have passed the test. All the test parameters are within the specified limit of assessment criteria.

### 4. Results, long version

- Plastic parts and terminals inspected before test for abnormalities like cracks, burrs, rust and breakage. All the samples subjected to test were in good/acceptable condition → OK

After the test Surfaces has no signs of rust – OK (See chapter 5.4 for Criteria)

### 5. Details

### 5.1 Part details:

Sl. No. | Description | Part number | Manufacture date / Received date | Remarks
1 | Vehicle Inlet | 340A0013634 | July-2022 | -
2 | Vehicle connector | 340A0021042 | July-2022 | -

### 5.2 Equipment details:

Sl. No. | Test equipment | Equipment no. | Remarks
1 | Saltwater setup | ATS-032 | Location: External lab (NABL - TC-7419)

### 5.3 Sample preparation, test setup and test details:

1. Visual inspection of plastic parts conducted on all the samples before test.
2. 3 samples of vehicle connector and vehicle inlet equipped with terminals are used for test.
3. All grease is removed from the parts to be tested, by immersion in ethyl acetone, acetone, methylethyl

ketone or an equivalent degreasing agent for 10 min.

4. Then the parts are then immersed for 10 min in a 10 percent solution of ammonium chloride in water at a

temperature of 20°C ± 5 K.

5. After that without drying, but after shaking off any drops, the parts are placed for 10 min in a box containing

air saturated with moisture at a temperature of 20°C ± 5 K.

6. After the parts have been dried for 10 min in a heating cabinet at a temperature of 100°C ± 5 K,
7. Same procedure was followed for all the other samples.
8. See pictures in chapter 6 Enclosure.

MS/ENB3 | Prijo Ulahannan | +91 80 6783 6100 | Prijo.ulahannan@in.bosch.com | Date: 18-Aug-2022 Report No.: Ather_01_TR


Page 3 of 4 Confidential | Test Report | © BGSW reserves all rights even in the event of industrial property rights.

### 5.4 Test conditions and assessment criteria:

Asessemnt Criteria:

After the test Surfaces has no signs of rust

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


Page 4 of 4 Confidential | Test Report | © BGSW reserves all rights even in the event of industrial property rights.

### 6. Enclosure

### 6.1 CORROSION AND RESISTANCE TO RUSTING

Pic 1: Test set up | Pic 2: Test set up

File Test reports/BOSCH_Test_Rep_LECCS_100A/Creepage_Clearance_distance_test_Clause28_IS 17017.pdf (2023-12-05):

From | Our reference | Phone | E-Mail
MS/ENB | Prijo Ulahannan | +91 80 6783 6100 | Prijo.ulahannan@in.bosch.com | Date: 22-Aug-2022 Report No.: Ather_07_TR
Page 1 of 6 Confidential | Test Report | © BGSW reserves all rights even in the event of industrial property rights.

We reserve all rights of disposal such as copying and passing on to third parties.
Report template V1 (05/25/2022)
R&D-Report: | Test report
Title: | Creepage and Clearance Distance Evaluation
Customer: | Ather India

Document approval

| Name | Signature
Prepared by | Prijo Ulahannan
Reviewed by | Mahantesh Ramannavar

### 1. Issues (situation, motivation and tasks)

The Ather Company has designed and developed a charging connector for electric vehicles, which is patented. Ather has approached Bosch (BGSW) to validate the charging connector between the vehicle and the charging station according to IS 17017 selective tests as prescribed by Ather requirements.

Creepage and Clearance Distances are required for the protection against the operating voltages to protect the equipment or user, moreover in case of malfunction of equipment. The criteria are as per IS 17017 chapter no.28.1, 28.3 & 28.4 to check the correct creep and clearance of the samples.

### 2. Results, short version

| | o.k. | not o.k.
2.1 | Evaluation of Creepage and Clearance Distance | ☒ | ☐

The overall result of the examined samples is:

☒ Positive
☐ Negative: No further analysis required

Recommendation for further work: NA

MS/ENB | Prijo Ulahannan | +91 80 6783 6100 | Prijo.ulahannan@in.bosch.com | Date: 22-Aug-2022 Report No.: Ather_07_TR
Page 2 of 6 Confidential | Test Report | © BGSW reserves all rights even in the event of industrial property rights.

### 3. Conclusions and consequences

All samples have passed the test. All the test parameters are within the specified limit of assessment criteria. From the sample cross section it is determined that the minimum clearance provided for the conducting or live parts are more than that of the required creepage and clearance as specified in the specifications. No electric breakdown and No damage on housings or terminals by deformations or melting observed after and withstand voltage test

### 4. Results, long version

4.1 Evaluation of creepage and clearance distances between live parts, with live parts with different polarity and other metallic accessories. → OK (See chapter 5.4 for criteria)

4.1.1 Creepage Distances and clearances in accordance to 28.1 | → OK
4.1.2 Conducting Evaluation is in accordance with IS 15382 part 1 | → OK

4.1.3 No burnt plastic parts were observed after and withstand voltage test (2000V and 50 Hz) → OK

### 5. Details

### 5.1 Part details:

Sl. No. | Description | Part number | Manufacture date / Received date | Remarks
1 | Vehicle Inlet Male and Female Connectors | ----- | August-2022 | -

### 5.2 Sample preparation, test setup and test details:

1. Accessories are designed as per pollution degree 3 according to IS 15382(Part 1).
2. Evaluation of creepage and clearance distance in accordance with IS 15382(Part 1).
3. Visually inspect and measure the shortest distance between live parts, with live parts of opposite polarity and other metal accessories in proximity if any.
4. From the sample cross section it is determined that the minimum clearance provided for the conducting or live parts are more than that of the required creepage and clearance as specified in the specifications

### 5.3 Test conditions and assessment criteria:

1. RMS Voltage Input: 100V.
2. Creepage distance to avoid tracking failure: 1.8 mm.
3. Clearance distance needed: 0.8 mm.
4. Accessories are under the Overvoltage category II.

MS/ENB | Prijo Ulahannan | +91 80 6783 6100 | Prijo.ulahannan@in.bosch.com | Date: 22-Aug-2022 Report No.: Ather_07_TR


Page 3 of 6 Confidential | Test Report | © BGSW reserves all rights even in the event of industrial property rights.

5.3.1 Data table for creepage distances to avoid tracking failure (IS 15382 (Part 1) :2003)

Note: The data marked in red box are of concern for determining the minimum expected Creepage and clearance distance.

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


Page 4 of 6 Confidential | Test Report | © BGSW reserves all rights even in the event of industrial property rights.

### 5.3.2 Data Table for Clearance Distances. (IS 15382 (Part 1) :2003)

Note: The data marked in red box are of concern for determining the minimum expected Creepage and clearance distance.

### 5.3.3 Material properties

1. Material Used: PA66 (DOMAMID FR66)
2. CTI Value of the Material being used: 600.
3. Material Group: I (According to the CTI value).

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


Page 5 of 6 Confidential | Test Report | © BGSW reserves all rights even in the event of industrial property rights.

### 6 Test Images

Inspection of sample connector terminal after test

Connector male part | Connector female part

Inspection of sample connector terminal after test

Connector male part | Connector female part

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

Reference Drawing; Clearance distances of terminals of; housing.; Clearances of the female plug end cross

Page 6 of 6 Confidential | Test Report | © BGSW reserves all rights even in the event of industrial property rights.

connector in proximity after mating with the section to be inserted to male live parts.

Withstand Voltage test set up

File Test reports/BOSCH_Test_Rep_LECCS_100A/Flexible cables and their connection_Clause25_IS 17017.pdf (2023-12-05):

From | Our reference | Phone | E-Mail
MS/ENB3 | Prijo Ulahannan | +91 80 6783 6100 | Prijo.ulahannan@in.bosch.com | Date: 18-Aug-2022 Report No.: Ather_02_TR
Page 1 of 4 Confidential | Test Report | © BGSW reserves all rights even in the event of industrial property rights.

We reserve all rights of disposal such as copying and passing on to third parties.
Report template V1 (05/25/2022)
Report: | Test report
Title: | Flexible cables and their connection
Customer: | Ather India

Document approval

| Name | Signature
Prepared by | Prijo Ulahannan
Reviewed by | Mahantesh Ramannavar

### 1. Issues (situation, motivation and tasks)

The Ather Company has designed and developed a charging connector for electric vehicles, which is patented. Ather has approached Bosch (BGSW) to validate the charging connector between the vehicle and the charging station according to IS 17017 selective tests as prescribed by Ather requirements.

Samples of vehicle connector used for test. The task was to perform pull test on samples, followed by a torque test to evalauate tensile strength of the cable with assembly. Test and acceptance criteria are as per IS 17017 chapter no. 25.3 to check the functionality of the samples.

### 2. Results, short version

| | o.k. | not o.k.
2.1 | Visual inspection of plastic parts for cracks and breakage (New condition) | ☒ | ☐
2.2 | Cable elongation/anchorage after the test | ☒ | ☐
2.3 | No break in electrical connection (Continuity check) after test | ☒ | ☐

The overall result of the examined samples is:

☒ Positive
☐ Negative: No further analysis required

Recommendation for further work: NA

MS/ENB3 | Prijo Ulahannan | +91 80 6783 6100 | Prijo.ulahannan@in.bosch.com | Date: 18-Aug-2022 Report No.: Ather_02_TR
Page 2 of 4 Confidential | Test Report | © BGSW reserves all rights even in the event of industrial property rights.

### 3. Conclusions and consequences

All connector samples have passed the test. All the test parameters are within the specified limit of assessment criteria.

### 4. Results, long version

- Plastic parts and terminals inspected before test for abnormalities like cracks, burrs, rust and breakage. All the samples subjected to test were in good/acceptable condition → OK

Cable elongation/anchorage after the test – OK (See chapter 5.4 for criteria)

Sl No. | Displacement
Sample - 1 | OK
Sample - 2 | OK
Sample - 3 | OK

No break in electrical connection (Continuity check) after test – OK (See chapter 5.4 for criteria)

Sl No. | Continuity Check
Sample - 1 | OK
Sample - 2 | OK
Sample - 3 | OK

### 5. Details

### 5.1 Part details:

Sl. No. | Description | Part number | Manufacture date / Received date | Remarks
1 | Vehicle connector | 340A0021042 | July-2022 | -

### 5.2 Equipment details:

Sl. No. | Test equipment | Equipment no. | Remarks
1 | UTM Machine | ATS-021 | Location: External lab (NABL - TC-7419)

MS/ENB3 | Prijo Ulahannan | +91 80 6783 6100 | Prijo.ulahannan@in.bosch.com | Date: 18-Aug-2022 Report No.: Ather_02_TR


Page 3 of 4 Confidential | Test Report | © BGSW reserves all rights even in the event of industrial property rights.

### 5.3 Sample preparation, test setup and test details:

1. Visual inspection of plastic parts conducted on all the samples before test.
2. 3 samples of vehicle connector assembly are used for the test.
3. The sample is fixed in the test apparatus so that the axis of the cable is vertical where it enters the sample
4. The cable is then subjected 100 times to a pull of the value shown in Table 18. Each pull is applied without

jerks and has a duration of 1s.

5. Immediately afterwards, the cable is subjected to a torque, of the value specified in Table 18.
6. The displacement of the mark on the cable in relation to the the cable anchorage is measured.
7. Continuity check is performed after the test.
8. Same procedure was followed for the all the other samples.
9. See pictures in chapter 6 Enclosure.

### 5.4 Test conditions and assessment criteria:

Asessemnt Criteria:

- During the tests, the cable shall not be damaged.
- After the tests, the cable shall not have been displaced by more than the values indicated in Table 18. (The displacement of the mark on the cable in relation to the the cable anchorage is measured)
- For non-rewirable accessories, there shall be no break in the electrical connections.


MS/ENB3 | Prijo Ulahannan | +91 80 6783 6100 | Prijo.ulahannan@in.bosch.com | Date: 18-Aug-2022 Report No.: Ather_02_TR
Page 4 of 4 Confidential | Test Report | © BGSW reserves all rights even in the event of industrial property rights.

### 6. Enclosure

### 6.1 Pictures

Pic 1: Test set up | Pic 2: Test set up

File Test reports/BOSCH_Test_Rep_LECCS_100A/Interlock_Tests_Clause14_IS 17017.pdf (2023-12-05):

From | Our reference | Phone | E-Mail
MS/ENB3 | Prijo Ulahannan | +91 80 6783 6100 | Prijo.ulahannan@in.bosch.com | Date: 18-Aug-2022 Report No.: Ather_05_TR
Page 1 of 7 Confidential | Test Report | © BGSW reserves all rights even in the event of industrial property rights.

We reserve all rights of disposal such as copying and passing on to third parties.
Report template V1 (05/25/2022)
Report: | Test report
Title: | Interlock withdrawal force test
Customer: | Ather India

Document approval

| Name | Signature
Prepared by | Prijo Ulahannan
Reviewed by | Mahantesh Ramannavar

### 1. Issues (situation, motivation and tasks)

The Ather Company has designed and developed a charging connector for electric vehicles, which is patented. Ather has approached Bosch (BGSW) to validate the charging connector between the vehicle and the charging station according to IS 17017 selective tests as prescribed by Ather requirements.

Samples of vehicle connector and vehicle inlet (With mechanical interlock) used for test were used for test. The task was to check the withdrawal force of the interlock with with specified force values. Test and acceptance criteria are as per IS 17017 chapter no.14.1.5 and 14.1.6 to check the functionality of the samples.

### 2. Results, short version

| | o.k. | not o.k.
2.1 | Visual inspection of plastic parts for cracks and breakage (New condition) | ☒ | ☐
2.2 | Test to check withdrawal force (Only plastic parts with interlock on vehicle inlet) | ☒ | ☐
2.3 | Withdrawal test with 90-degree rotation (Vehicle connector and inlet assembly) | ☒ | ☐

The overall result of the examined samples is:

☒ Positive
☐ Negative: No further analysis required

Recommendation for further work: NA

MS/ENB3 | Prijo Ulahannan | +91 80 6783 6100 | Prijo.ulahannan@in.bosch.com | Date: 18-Aug-2022 Report No.: Ather_05_TR
Page 2 of 7 Confidential | Test Report | © BGSW reserves all rights even in the event of industrial property rights.

### 3. Conclusions and consequences

All connector samples have passed the test. All the test parameters are within the specified limit of assessment criteria.

### 4. Results, long version

- Plastic parts and terminals inspected before test for abnormalities like cracks, burrs, rust and breakage. All the samples subjected to test were in good/acceptable condition → OK

4.1 Test to check withdrawal force (Only plastic parts with mechanical interlock on vehicle inlet) - OK

(See chapter 5.4 for criteria)

Sample - 1 | OK
Sample - 2 | OK
Sample - 3 | OK

### 4.2 Withdrawal test with 90-degree rotation (Vehicle connector and inlet assembly) – OK

(See chapter 5.4 for criteria)

Sample - 1 | OK
Sample - 2 | OK
Sample - 3 | OK

### 5. Details

### 5.1 Part details:

Sl. No. | Description | Part number | Manufacture date / Received date | Remarks
1 | Vehicle Inlet (With locking) | 340A0013634 | July-2022 | -
2 | Vehicle connector | 340A0021042 | July-2022 | -
3 | Vehicle connector (Only plastic) | 340A0003338 | July-2022 | -

### 5.2 Equipment details:

Sl. No. | Test equipment | Equipment no. | Remarks
1 | UTM | ENB/CL/002-1027832 | Location: BGSW

MS/ENB3 | Prijo Ulahannan | +91 80 6783 6100 | Prijo.ulahannan@in.bosch.com | Date: 18-Aug-2022 Report No.: Ather_05_TR


Page 3 of 7 Confidential | Test Report | © BGSW reserves all rights even in the event of industrial property rights.

### 5.3 Sample preparation, test setup and test details:

5.3.1 Test to check withdrawal force (Only plastic parts with mechanical interlock on vehicle inlet)

1. Visual inspection of plastic parts conducted on all the samples before test.
2. 3 samples of vehicle inlets and vehicle connectors are used for test.
3. The connector is inserted into and withdrawn ten times.
4. The connector with interlock is fixed to the support of an apparatus so that the axis of separation is

vertical and the movement is downwards (See chapter 6 for pictures)

5. A force equal to one-tenth of the withdrawal force as per table 9 (See chapter 5.4) is apllied and

maintained for 60s.

6. Same procedure was followed for the all the other samples.

### 5.3.2 Withdrawal test with 90-degree rotation (Vehicle connector and inlet assembly)

1. Visual inspection of plastic parts conducted on all the samples before test.
2. 3 samples of vehicle inlets and vehicle connectors are used for test.
3. The connector is inserted into and withdrawn ten times.
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

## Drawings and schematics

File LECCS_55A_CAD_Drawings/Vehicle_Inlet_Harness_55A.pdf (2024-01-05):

### CONNECTOR DETAILS: 4 PIN-FEMALE

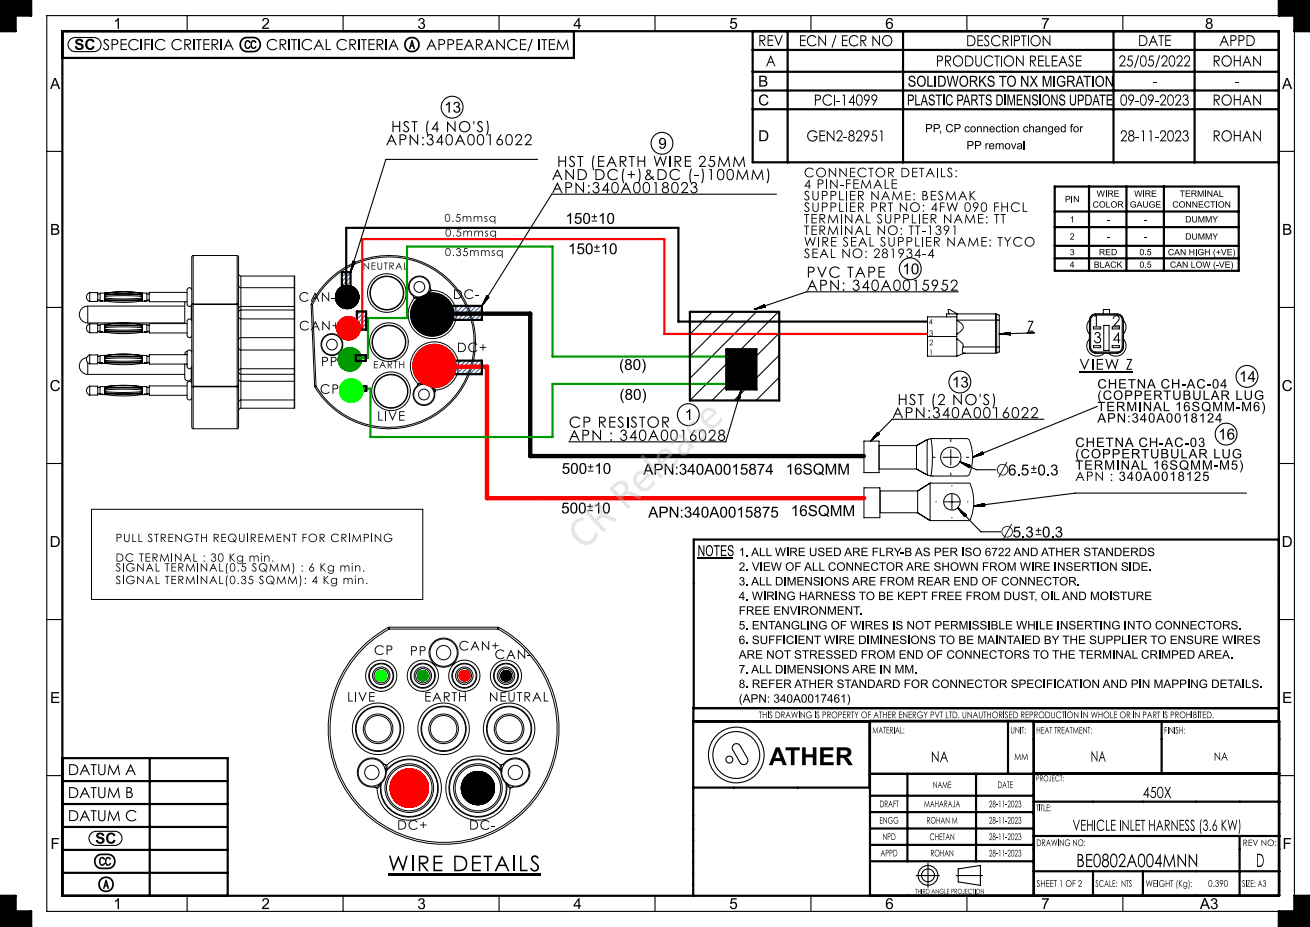
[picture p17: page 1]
CHETNA CH-AC-04 (COPPERTUBULAR LUG TERMINAL 16SQMM-M6) APN:340A0018124; HST (2 NO'S) APN:340A0016022; (COPPERTUBULAR; LUG; WIRE DETAILS; CP RESISTOR APN : 340A0016028; HST (4 NO'S) APN:340A0016022; CAN+CAN-; LIVE; EARTH; NEUTRAL; VIEW Z; DATUM A; DATUM B; DATUM C; NOTES; REV ECN / ECR NO; DESCRIPTION; DATE; APPD; PRODUCTION RELEASE; ROHAN; SOLIDWORKS TO NX MIGRATION; PCI-14099; PLASTIC PARTS DIMENSIONS UPDATE 09-09-2023; GEN2-82951; PIN; WIRE; COLOR; WIRE GAUGE; TERMINAL CONNECTION; DUMMY; RED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

SPECIFIC CRITERIA CRITICAL CRITERIA Ⓐ APPEARANCE/ ITEM

PP, CP connection changed for

HST (EARTH WIRE 25MM
AND DC(+)&DC (-)100MM)
APN:340A0018023

SUPPLIER NAME: BESMAK
SUPPLIER PRT NO: 4FW 090 FHCL
TERMINAL SUPPLIER NAME: TT
TERMINAL NO: TT-1391
WIRE SEAL SUPPLIER NAME: TYCO
SEAL NO: 281934-4
PVC TAPE
APN: 340A0015952

CHETNA CH-AC-03
TERMINAL 16SQMM-M5)
APN : 340A0018125

PULL STRENGTH REQUIREMENT FOR CRIMPING
DC TERMINAL : 30 Kg min.
SIGNAL TERMINAL(0.5 SQMM) : 6 Kg min.
SIGNAL TERMINAL(0.35 SQMM): 4 Kg min.

1. ALL WIRE USED ARE FLRY-B AS PER ISO 6722 AND ATHER STANDERDS
2. VIEW OF ALL CONNECTOR ARE SHOWN FROM WIRE INSERTION SIDE.
3. ALL DIMENSIONS ARE FROM REAR END OF CONNECTOR.
4. WIRING HARNESS TO BE KEPT FREE FROM DUST, OIL AND MOISTURE
FREE ENVIRONMENT.
5. ENTANGLING OF WIRES IS NOT PERMISSIBLE WHILE INSERTING INTO CONNECTORS.
6. SUFFICIENT WIRE DIMINESIONS TO BE MAINTAIED BY THE SUPPLIER TO ENSURE WIRES
ARE NOT STRESSED FROM END OF CONNECTORS TO THE TERMINAL CRIMPED AREA.
7. ALL DIMENSIONS ARE IN MM.
8. REFER ATHER STANDARD FOR CONNECTOR SPECIFICATION AND PIN MAPPING DETAILS.
(APN: 340A0017461)

THIS DRAWING IS PROPERTY OF ATHER ENERGY PVT LTD. UNAUTHORISED REPRODUCTION IN WHOLE OR IN PART IS PROHIBITED.
ATHER

TITLE:
VEHICLE INLET HARNESS (3.6 KW)

THIRD ANGLE PROJECTION

## DC TERMINAL VEHICLE INLET

## 16 SQMM (2 NO'S)

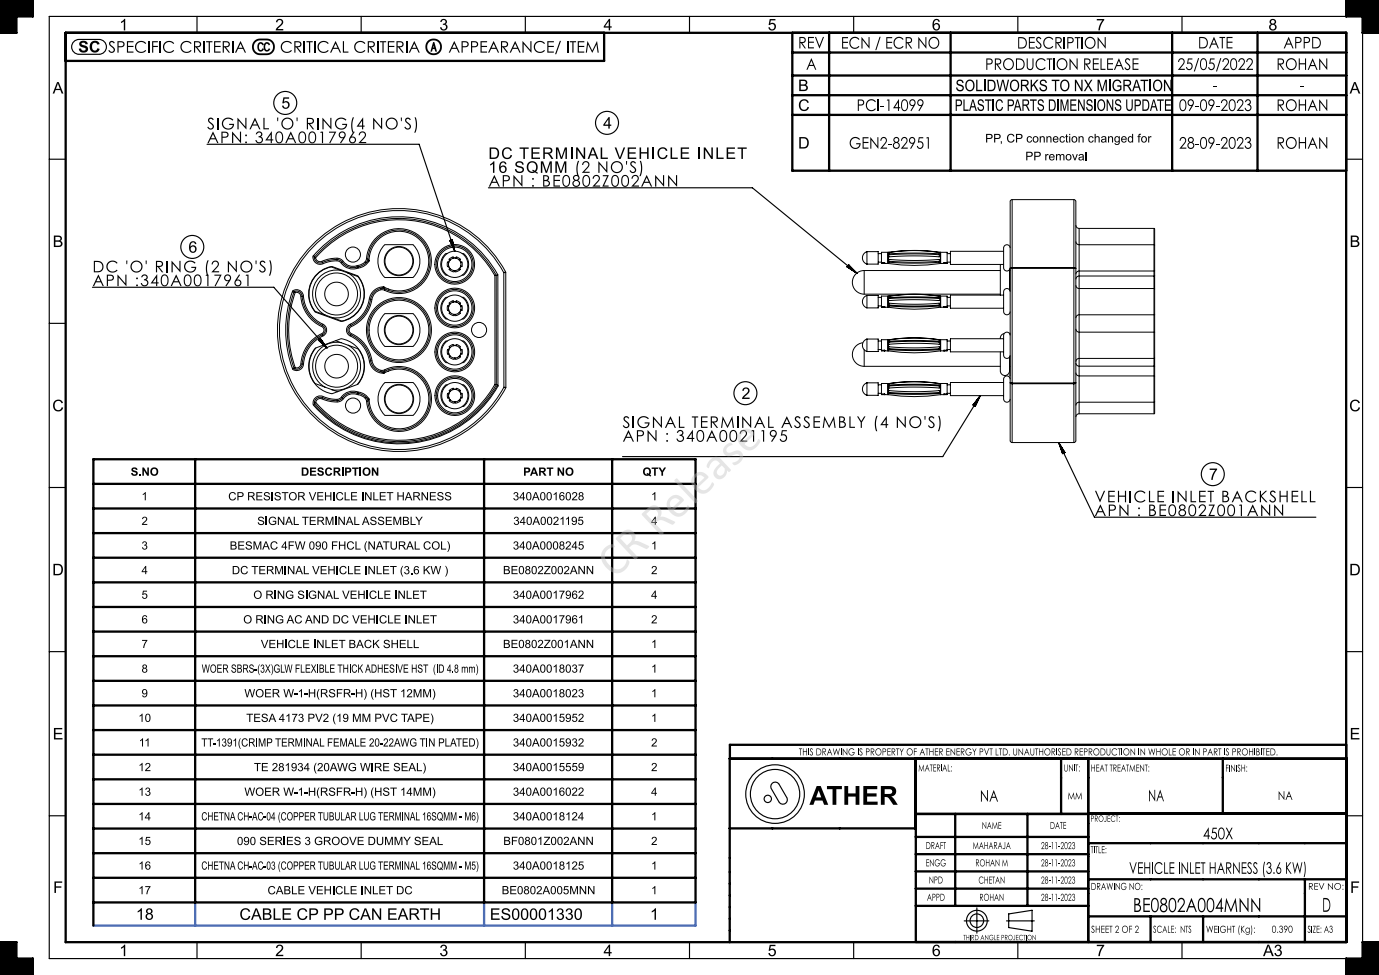
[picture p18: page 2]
APN : BE0802Z002ANN; DC 'O' RING (2 NO'S) APN :340A0017961; REV ECN / ECR NO; DESCRIPTION; DATE; APPD; PRODUCTION RELEASE; ROHAN; SOLIDWORKS TO NX MIGRATION; PCI-14099; PLASTIC PARTS DIMENSIONS UPDATE 09-09-2023; GEN2-82951; PP removal; HEAT TREATMENT:; FINISH:; MATERIAL:; UNIT:; NAME; DRAFT; MAHARAJA; ENGG; ROHAN M; NPD; CHETAN; PROJECT:; DRAWING NO:; REV NO:; BE0802A004MNN; SHEET 2 OF 2; SCALE: NTS; WEIGHT (Kg):; SIZE: A3; PART NO; QTY; CP RESISTOR VEHICLE INLET HARNESS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

SPECIFIC CRITERIA CRITICAL CRITERIA Ⓐ APPEARANCE/ ITEM

SIGNAL 'O' RING(4 NO'S)
APN: 340A0017962

PP, CP connection changed for

SIGNAL TERMINAL ASSEMBLY (4 NO'S)
APN : 340A0021195

VEHICLE INLET BACKSHELL
APN : BE0802Z001ANN

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

TITLE:
VEHICLE INLET HARNESS (3.6 KW)

THIRD ANGLE PROJECTION

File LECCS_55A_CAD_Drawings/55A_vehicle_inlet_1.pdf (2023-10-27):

# PVC TAPE APN: 340A0015952

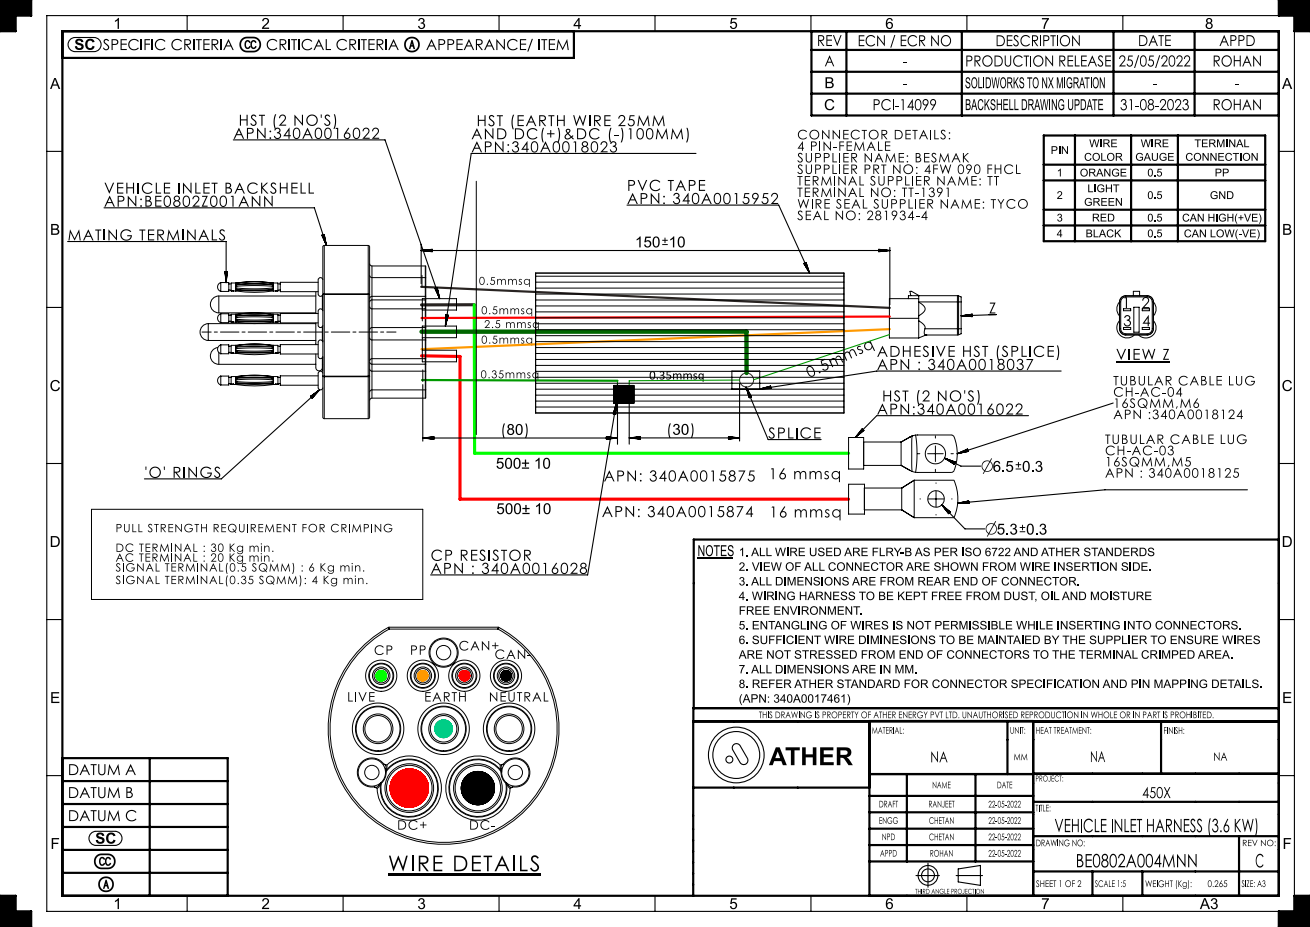
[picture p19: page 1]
HST (2 NO'S) APN:340A0016022; 16 mmsq; 2.5 mmsq; APN: 340A0015875; APN: 340A0015874; (80) SPLICE; WIRE DETAILS; 0.5mmsq; CP RESISTOR APN : 340A0016028; ADHESIVE; HST (SPLICE); APN : 340A0018037; CAN+CAN-; LIVE; EARTH; NEUTRAL; 0.35mmsq; 'O' RINGS; MATING TERMINALS; VIEW Z; MATERIAL:; UNIT:; HEAT TREATMENT:; FINISH:; PROJECT:; DRAWING NO:; REV NO:; BE0802A004MNN; SHEET 1 OF 2; SCALE 1:5; WEIGHT (Kg):; SIZE: A3; NAME; DATE; DRAFT; RANJEET; ENGG; CHETAN; NPD; APPD; ROHAN; DATUM A; DATUM B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

SPECIFIC CRITERIA CRITICAL CRITERIA Ⓐ APPEARANCE/ ITEM

HST (EARTH WIRE 25MM
AND DC(+)&DC (-)100MM)
APN:340A0018023

CONNECTOR DETAILS:
4 PIN-FEMALE
SUPPLIER NAME: BESMAK
SUPPLIER PRT NO: 4FW 090 FHCL
TERMINAL SUPPLIER NAME: TT
TERMINAL NO: TT-1391
WIRE SEAL SUPPLIER NAME: TYCO
SEAL NO: 281934-4

VEHICLE INLET BACKSHELL
APN:BE0802Z001ANN

TUBULAR CABLE LUG
16SQMM,M6
APN :340A0018124
16SQMM,M5
APN : 340A0018125

PULL STRENGTH REQUIREMENT FOR CRIMPING
DC TERMINAL : 30 Kg min.
AC TERMINAL : 20 Kg min.
SIGNAL TERMINAL(0.5 SQMM) : 6 Kg min.
SIGNAL TERMINAL(0.35 SQMM): 4 Kg min.

1. ALL WIRE USED ARE FLRY-B AS PER ISO 6722 AND ATHER STANDERDS
2. VIEW OF ALL CONNECTOR ARE SHOWN FROM WIRE INSERTION SIDE.
3. ALL DIMENSIONS ARE FROM REAR END OF CONNECTOR.
4. WIRING HARNESS TO BE KEPT FREE FROM DUST, OIL AND MOISTURE
FREE ENVIRONMENT.
5. ENTANGLING OF WIRES IS NOT PERMISSIBLE WHILE INSERTING INTO CONNECTORS.
6. SUFFICIENT WIRE DIMINESIONS TO BE MAINTAIED BY THE SUPPLIER TO ENSURE WIRES
ARE NOT STRESSED FROM END OF CONNECTORS TO THE TERMINAL CRIMPED AREA.
7. ALL DIMENSIONS ARE IN MM.
8. REFER ATHER STANDARD FOR CONNECTOR SPECIFICATION AND PIN MAPPING DETAILS.
(APN: 340A0017461)

THIS DRAWING IS PROPERTY OF ATHER ENERGY PVT LTD. UNAUTHORISED REPRODUCTION IN WHOLE OR IN PART IS PROHIBITED.
ATHER

TITLE:
VEHICLE INLET HARNESS (3.6 KW)

THIRD ANGLE PROJECTION

# DC TERMINAL VEHICLE INLET (2 NO'S) APN : BE0802Z002ANN

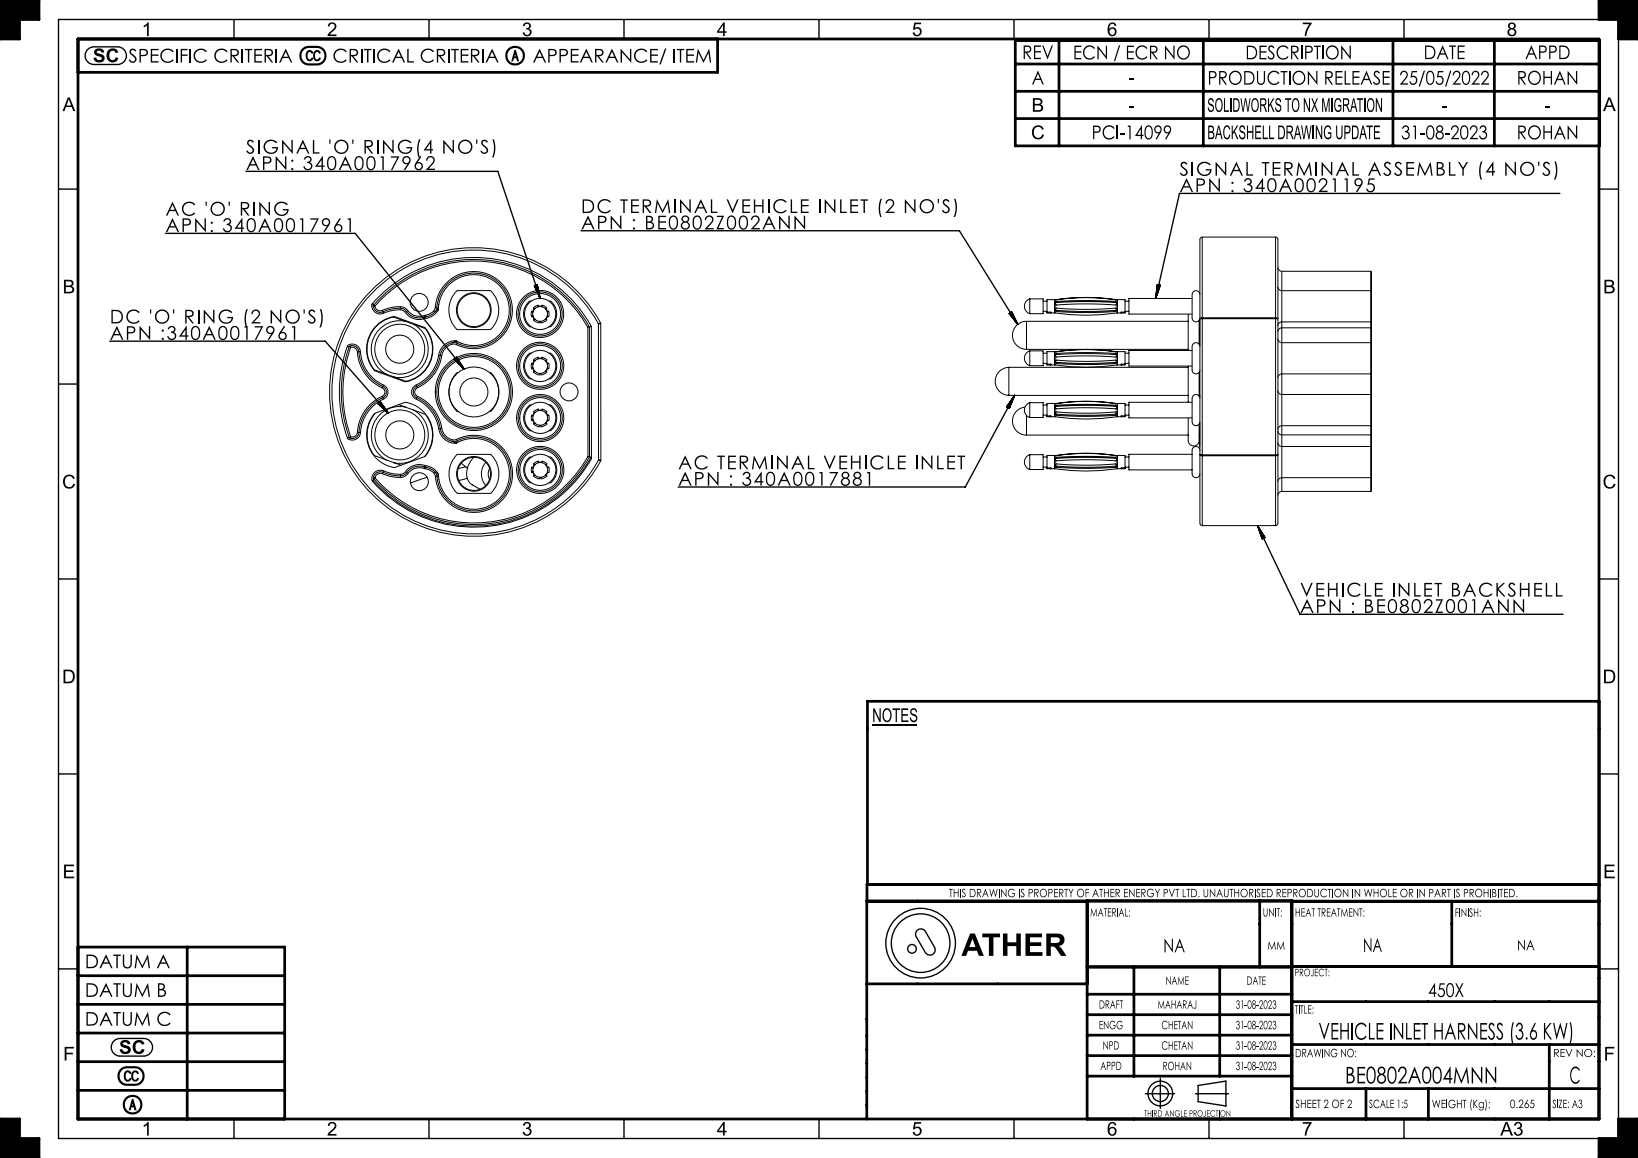
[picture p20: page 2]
AC 'O' RING APN: 340A0017961; DC 'O' RING (2 NO'S) APN :340A0017961; DATUM C; NOTES; HEAT TREATMENT:; FINISH:; SHEET 2 OF 2; SCALE 1:5; WEIGHT (Kg):; SIZE: A3; DRAFT; MAHARAJ; ENGG; CHETAN; NPD; APPD; ROHAN; REV; ECN / ECR NO; DESCRIPTION; DATE; PCI-14099; BACKSHELL DRAWING UPDATE

SPECIFIC CRITERIA CRITICAL CRITERIA Ⓐ APPEARANCE/ ITEM

A | - | PRODUCTION RELEASE | | 25/05/2022 | ROHAN
B | - | SOLIDWORKS TO NX MIGRATION | - | -

SIGNAL 'O' RING(4 NO'S)
APN: 340A0017962

SIGNAL TERMINAL ASSEMBLY (4 NO'S)
APN : 340A0021195

AC TERMINAL VEHICLE INLET
APN : 340A0017881

VEHICLE INLET BACKSHELL
APN : BE0802Z001ANN

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

MATERIAL: NA | UNIT: MM | NA | NA

DATUM A
DATUM B

NAME | DATE | | PROJECT: 450X

TITLE:
VEHICLE INLET HARNESS (3.6 KW)

DRAWING NO: BE0802A004MNN | REV NO: C

THIRD ANGLE PROJECTION

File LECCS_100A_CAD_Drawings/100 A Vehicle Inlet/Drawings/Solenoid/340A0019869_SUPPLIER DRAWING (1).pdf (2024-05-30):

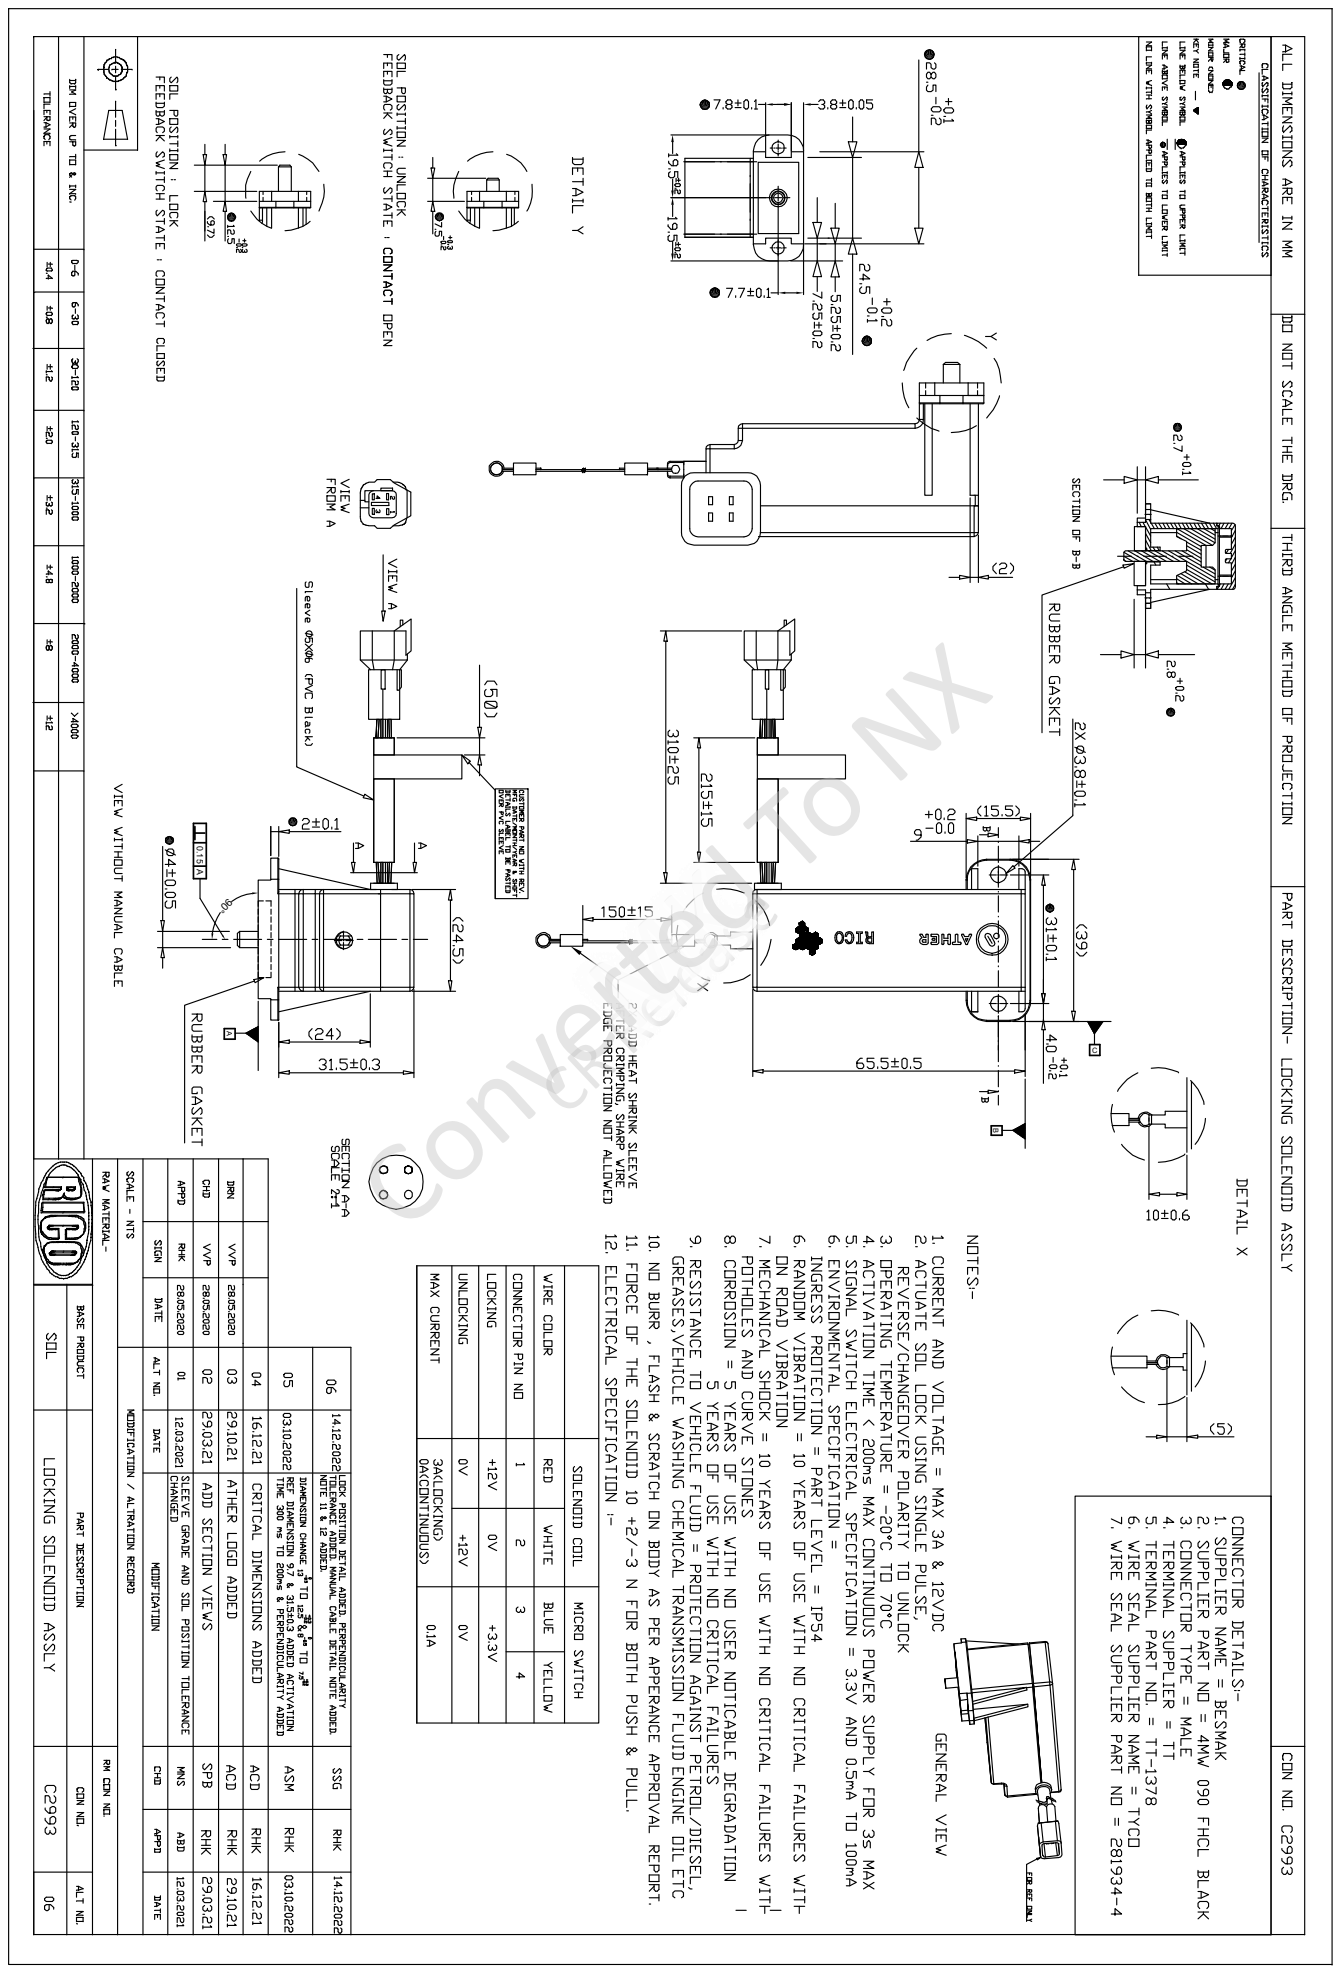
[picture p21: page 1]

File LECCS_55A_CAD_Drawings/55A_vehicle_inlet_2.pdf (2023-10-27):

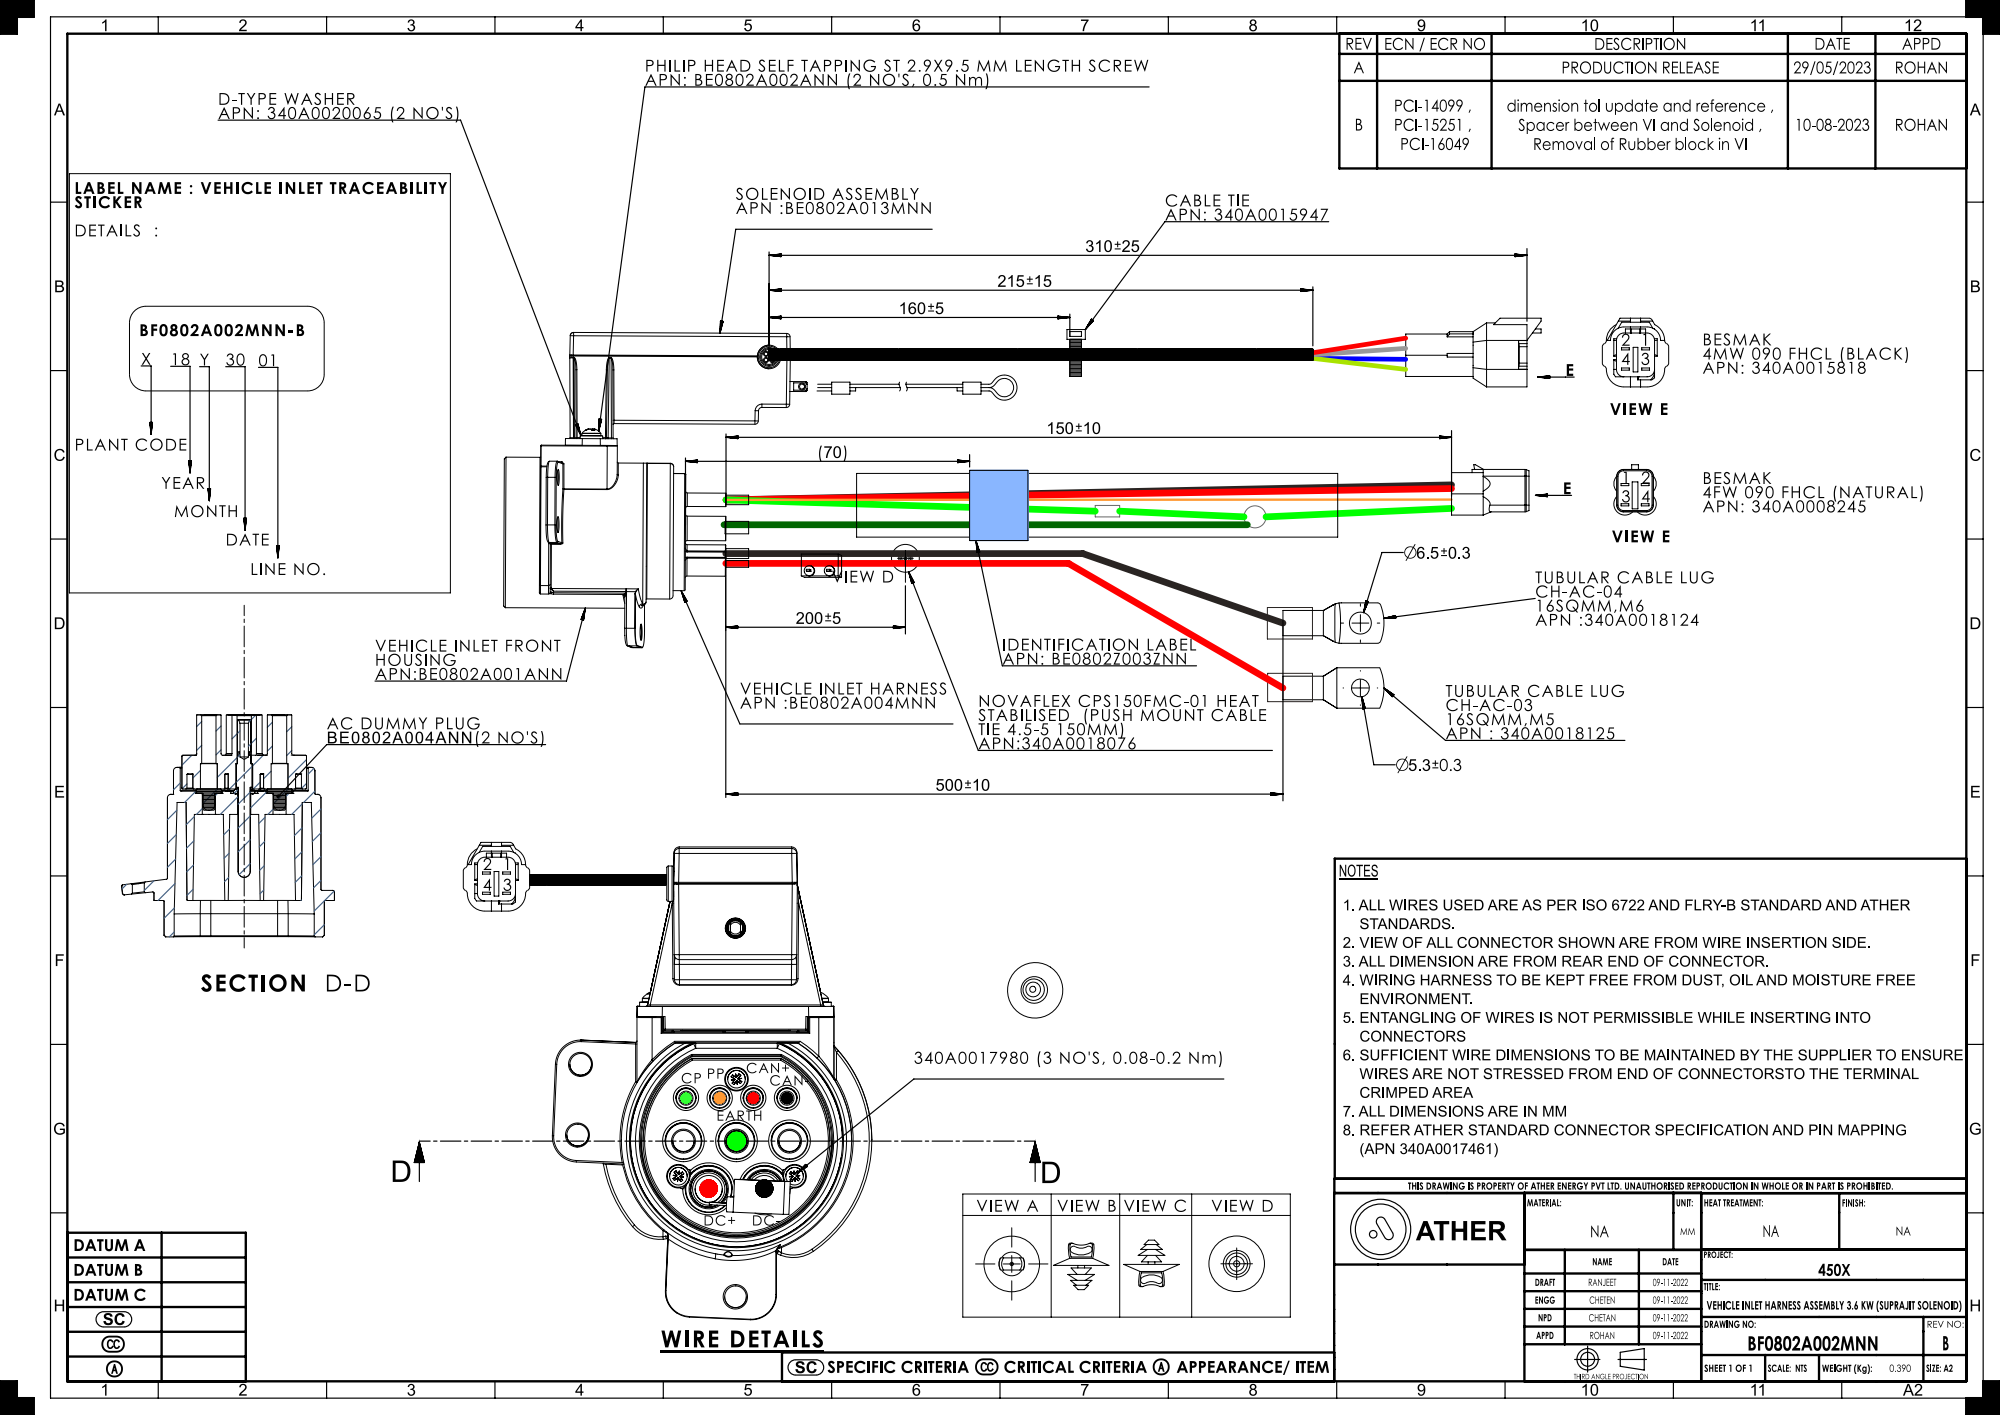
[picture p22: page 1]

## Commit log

2023-10-27 Upload of 55A vehicle inlet CAD, harness drawings
2023-11-27 Added 55 Amp handle CAD
2023-11-30 Added 55A charging handle assembly step with corrected CAD
2024-01-05 Added 100A charging handle and drawings. Added 55A Vehicle inlet harness drawing
2024-01-08 adding solenoid actuator drawing, with permission from Vendor confirmed
2024-01-24 Added in solenoid engineering spec sheet. Cleaned up some duplicate files
    [Solenoid_eng_spec_sheet_rev1.xlsx]
2024-01-31 vehicle inlet CAD and drawings attached
2024-03-01 LECCS 100A CAD and drawings added and restructured
    [Solenoid_eng_spec_sheet_rev1.xlsx]
2024-05-30 Added modifications to charging handle grommet, added charging handle surface files, modified charging handle harness drawings, updated drawings for vehicle inlet terminal
    [BE5101A004ANN_D_STEP (1).stp, EP00000127_03_STEPSelected_Objs.stp, Handle surface.igs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]
2024-09-27 Adding in a folder for Prototype parts, Added 100A charging handle and connector proto CAD files
2024-11-21 Added in a prototype for 100A Vehicle inlet assembly in protos folder

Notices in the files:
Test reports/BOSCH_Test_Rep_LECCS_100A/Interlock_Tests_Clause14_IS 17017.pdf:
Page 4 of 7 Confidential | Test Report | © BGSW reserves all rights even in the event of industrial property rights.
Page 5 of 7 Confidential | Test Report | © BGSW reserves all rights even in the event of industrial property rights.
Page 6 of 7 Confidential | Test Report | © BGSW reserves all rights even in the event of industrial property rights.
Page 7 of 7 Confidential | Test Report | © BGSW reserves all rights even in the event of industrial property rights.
